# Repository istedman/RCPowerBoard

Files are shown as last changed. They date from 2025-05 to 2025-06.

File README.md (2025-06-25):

# RCPowerBoard

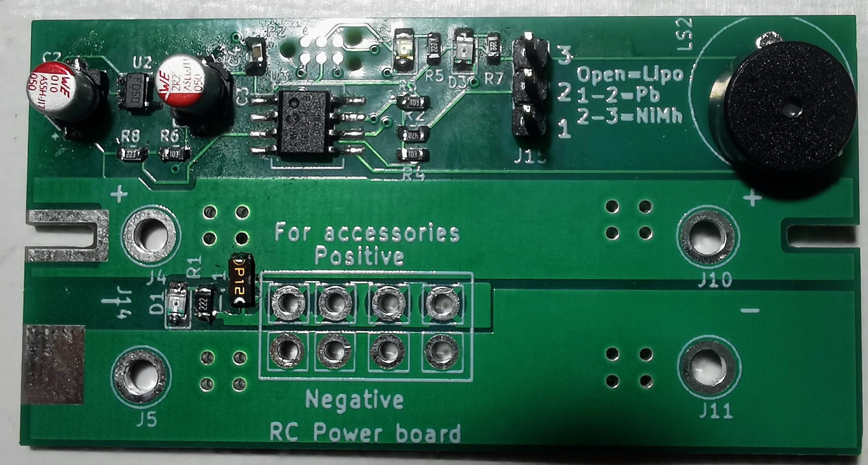
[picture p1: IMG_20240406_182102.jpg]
Photo of the PCB


A power distribution and battery monitor PCB for radio control vehicles. It can handle up to 15A, I use it on my smaller boats without issue.
Power connections are via plated through-hole or deans/T connectors. There are 4 pairs of smaller holes, connected via a 3.15A polyfuse, for accessory circuits. This protects the battery from short circuits in the accessory devices.

A PIC12F1840 microcontroller monitors the battery/cell voltages and when it gets too low, a buzzer will sound to let you know.

## Supported battery types

4-8 cell NiMh
1-3 cell Lipo
6V or 12V lead acid.

## Software
The design is minimal. A jumper identifies the battery type to monitor, providing you set this with a freshly charged battery pack, it will correctly determine the cell count and store the required settings in EEPROM. Only needs to be done once.
The BatteryMonitor.X directory contains the full source code, exported from MPLabX 6.20

**The software is designed to monitor the battery pack to these lower levels:**
_Lithium Polymer (LiPo)_
Single cell (1S) Lipo    3.6V
Duall cell (2S) Lipo     7.2V
Triple cell (3S) Lipo    10.8V
#define TRIPLE_LIPO_HIGH    12.600     // 12.6V

_Lead acid/AGM cell voltages_
 100% 2.12-2.15V per cell
 20% 1.93V/cell
 0% 1.75V/cell
 We will warn at 20% or 1.93V/cell
6V lower limit is  5.790V
12V lower limit is 11.580V     

_NiMH battery packs_
4 Cell NiMh    4.000V
5 Cell NiMh    5.000V    
6 Cell NiMh    6.00V
7 Cell NiMh    7.00V
8 Cell NiMh    8.00V

The software uses the internal A/D converter of the PIC microcontroller to sample the cell voltage, average it and if it drops below the limits detailed above, it will sound the buzzer. The A/D sampling is at a low rate, this was found to be effective in filtering out momentary supply blips when they accured, eliminating false failures.

Microchip Code Configurator (MCC) was used to setup the device and calibrate the internal voltage reference.

**Measured accuracy has been +/- 0.8% at room temperature** the 1% resistors used in the potential divider, contribute to the error in measurement, which was around 80mV in a 14V range.

## Known issues

The MCP2030 programming header is wrong, I had to swap signals around, will fix it in the next PCB iteration.
The deans/T connector footprint is off, again will be fixed in next revision.
The software only supports Nimh cells with even number of cells.
The PCB is bigger than it needs to be. I have 25 PCBs so there is no rush to fix the design, yet.

## Future development
A new, smaller design is in development that just monitors the battery and supports a wider range of chemistries/types. It can operate from a single cell Lipo or 3 NiMh cells. Plan to publish this later in the year, when finished.

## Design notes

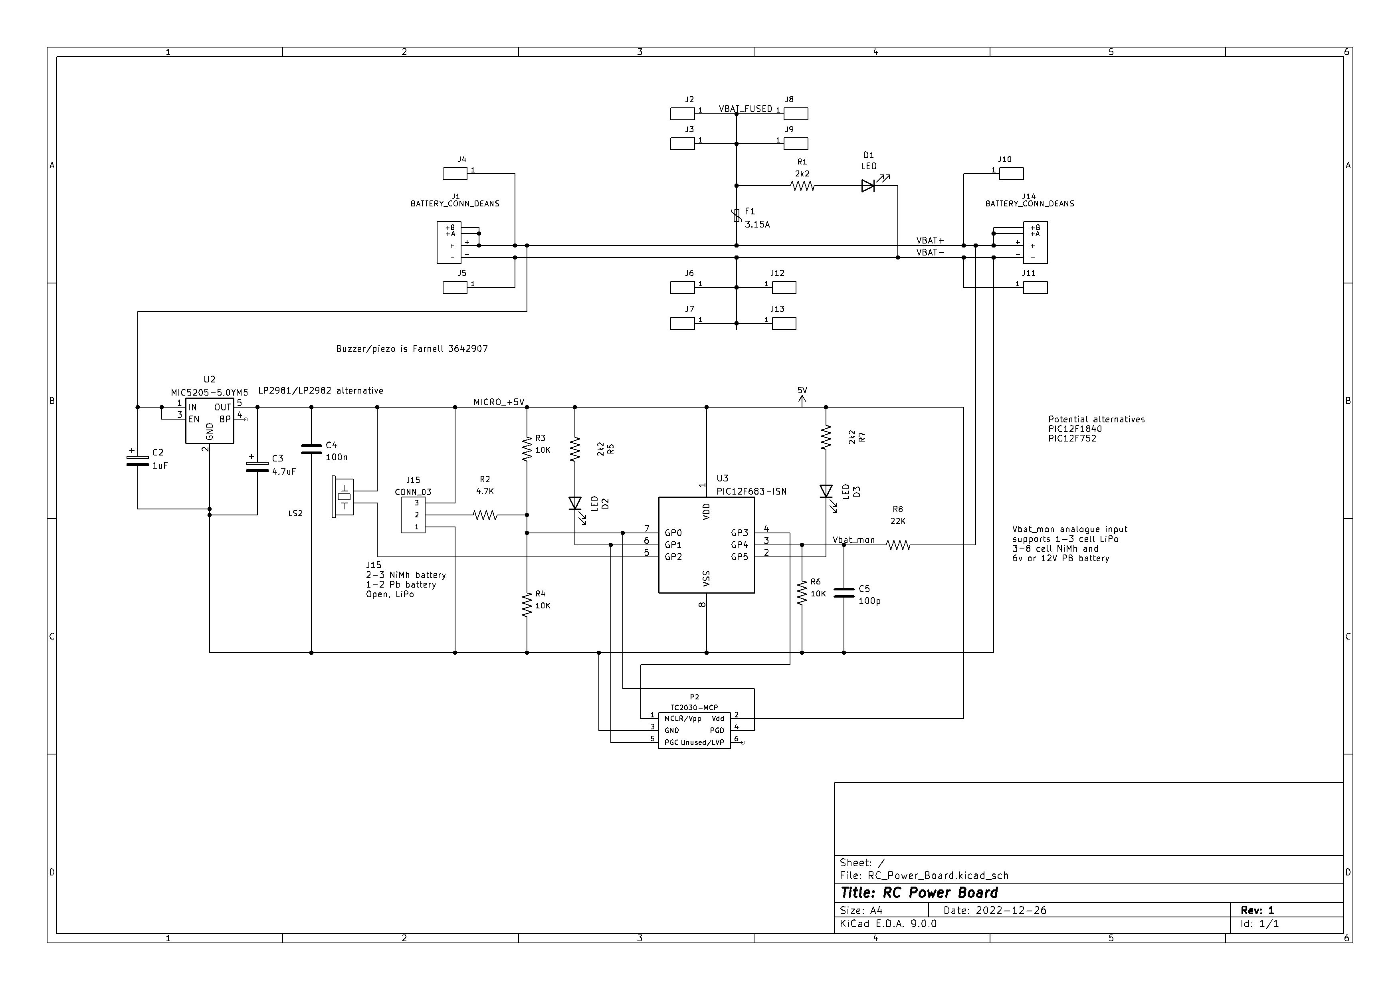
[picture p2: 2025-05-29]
RC_Power_board_schematic.jpg

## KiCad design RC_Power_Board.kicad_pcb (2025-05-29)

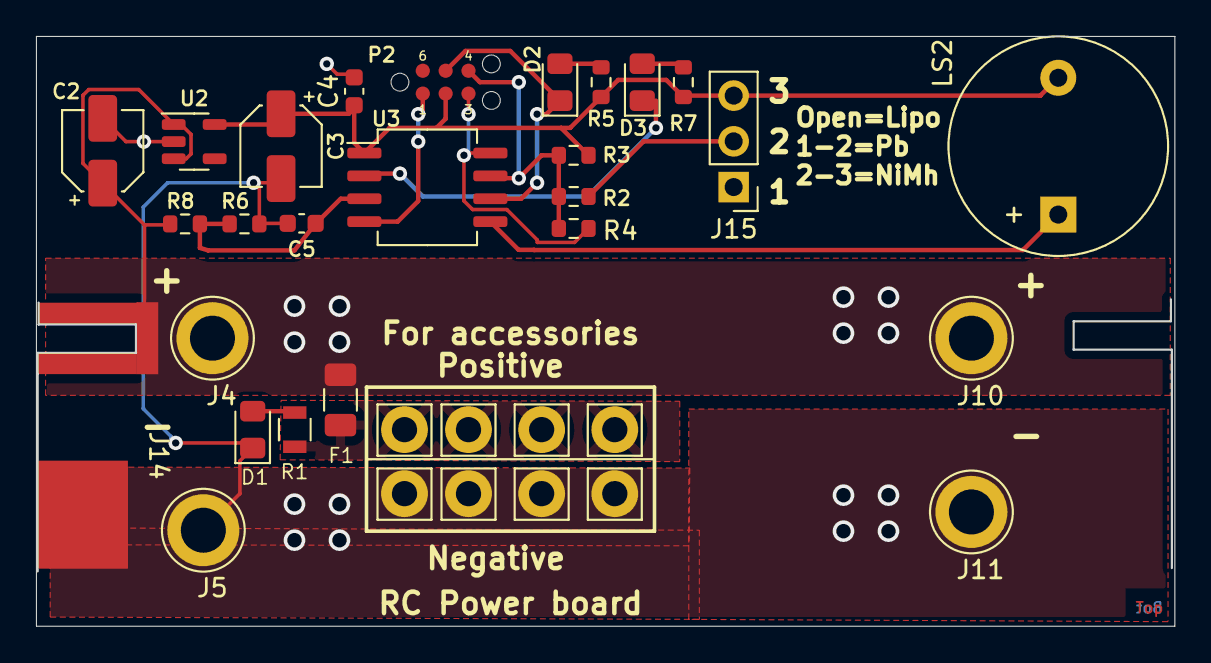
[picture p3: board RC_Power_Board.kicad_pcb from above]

Board: 2 copper layers, 63.2 x 32.8 mm, 35 parts (1 on the bottom side), 14 nets.

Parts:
C2: 1uF; CP_Elec_4x5.4
C3: 4.7uF; CP_Elec_4x5.4
C4: 100n; C_0603_1608Metric
C5: 100p; C_0603_1608Metric
D1, D2, D3: LED; LED_0805_2012Metric_Pad1.15x1.40mm_HandSolder
F1: 3.15A; Fuse_1206_3216Metric
J1, J14: BATTERY_CONN_DEANS; Deans_PCB
J2, J3, J6, J7, J8, J9, J12, J13: CONN_01POGOPIN_HOLE_LARGE; Pin_D1.4mm_L8.5mm_W2.8mm_FlatFork
J4, J5, J10, J11: CONN_01POGOPIN_HOLE_LARGE; TestPoint_Loop_D3.80mm_Drill2.5mm
J15: CONN_03; PinHeader_1x03_P2.54mm_Vertical
LS2: BUZZER-PTH; Buzzer_12x9.5RM7.6
P2: TC2030-MCP; TC2030-IDC-NL
R1: 2k2; R_0805
R2: 1K; R_0603_1608Metric
R3, R4, R6: 10K; R_0603_1608Metric
R5, R7: 2k2; R_0603_1608Metric
R8: 22K; R_0603_1608Metric
U2: MIC5205-5.0YM5; SOT-23-5
U3: PIC12F683-ISN; SO-8_5.3x6.2mm_P1.27mm

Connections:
/MICRO_+5V: C3.1, C4.1, J15.3, LS2.2 (-), P2.2 (Vdd), R3.2, R5.1, R7.1, U2.5 (OUT), U3.1 (VDD)
/VBAT+: C2.1, F1.2, J1.+, J4.1, J10.1, J14.+, R8.2, U2.1 (IN), U2.3 (EN)
/VBAT-: C2.2, C3.2, C4.2, C5.2, D1.1 (K), J1.-, J5.1, J6.1, J7.1, J11.1, J12.1, J13.1, J14.-, J15.1, P2.3 (GND), R4.1, R6.1, U2.2 (GND), U3.8 (VSS)
/VBAT_FUSED: F1.1, J2.1, J3.1, J8.1, J9.1, R1.1
/Vbat_mon: C5.1, R6.2, R8.1, U3.3 (GP4)
unnamed: D1.2 (A), R1.2
unnamed: D2.1 (K), P2.5 (PGC), U3.6 (GP1)
unnamed: D2.2 (A), R5.2
unnamed: D3.1 (K), U3.2 (GP5)
unnamed: D3.2 (A), R7.2
unnamed: J15.2, R2.2
unnamed: LS2.1 (+), U3.5 (GP2)
unnamed: P2.1 (MCLR/Vpp), U3.4 (GP3)
unnamed: P2.4 (PGD), R2.1, R3.1, R4.2, U3.7 (GP0)

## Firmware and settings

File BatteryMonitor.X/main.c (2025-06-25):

/**
  Generated Main Source File

  Company:
    Microchip Technology Inc.

  File Name:
    main.c

  Summary:
    This is the main file generated using PIC10 / PIC12 / PIC16 / PIC18 MCUs

  Description:
    This header file provides implementations for driver APIs for all modules selected in the GUI.
    Generation Information :
        Product Revision  :  PIC10 / PIC12 / PIC16 / PIC18 MCUs - 1.81.7
        Device            :  PIC12F1840
        Driver Version    :  2.00
*/


#include "mcc_generated_files/mcc.h"

#define LED1        LATAbits.LATA1  // RA0 is LED for debugging purposes
#define LED2        LATAbits.LATA5  // RA1 is second debug LED
#define BUZZER      LATAbits.LATA2
#define LEDON  0
#define LEDOFF 1
#define BUZZON 0
#define BUZZOFF 1
#define BUZZERON 10

//EEPROM locations
const unsigned char BAT_TYPE_STORE_LOC=0;
const unsigned char BAT_CELL_STORE_LOC=1;
#define BAT_TYPE_LIPO 0x10
#define BAT_TYPE_NIMH 0x20
#define BAT_TYPE_LEAD 0x30

//Initialise it for LIPO 2 Cell in EEPROM
__EEPROM_DATA(30,02,00,00,00,00,00,55);  

/*
 Based on 16V battery input range and a 10 bit ADC, the effective resolution is 15.625mV/bit
 The voltage seen at ADC input is 0.3125x the input voltage
 The Battery type analogue input uses the standard 4.88mV/bit resolution.
 * 
 */
// Might need to tweak single cell LiPO to use internal reference
#define SINGLE_LIPO_LOW     3.600     // 3.6V
#define SINGLE_LIPO_HIGH    4.250     // 4.25V
#define DUAL_LIPO_LOW       7.200     // 7.2V
#define DUAL_LIPO_HIGH      8.450     // 8.45V
#define TRIPLE_LIPO_LOW     10.800     // 10.8V
#define TRIPLE_LIPO_HIGH    12.600     // 12.6V

/* 
 Lead acid/AGM cell voltages
 * 100% 2.12-2.15V per cell
 * 20% 1.93V/cell
 * 0% 1.75V/cell
 * We will warn at 20% or 1.93V/cell
 */

#define LEAD_ACID_6V_LOW    5.790
#define LEAD_ACID_6V_HIGH   6.450    
#define LEAD_ACID_12V_LOW   11.580     
#define LEAD_ACID_12V_HIGH  12.900    


/* Might need to tweak 4 & 5 cell NiMh to use internal reference
 * Use 1.4V x number of cells for upper limit for battery detection
 * Use 1.2V for lower limit for detection, this is 50% charge for a cell
 * Use 1.0V x number of cells for lower limit 
 */

#define NIMH_4CELL_LOW      4.000    
#define NIMH_4CELL_DET_LOW  4.800
#define NIMH_4CELL_HIGH     5.600     

#define NIMH_5CELL_LOW      5.000    
#define NIMH_5CELL_DET_LOW  6.000
#define NIMH_5CELL_HIGH     7.000     

#define NIMH_6CELL_LOW      6.000     
#define NIMH_6CELL_DET_LOW  7.200
#define NIMH_6CELL_HIGH     8.400     

#define NIMH_7CELL_LOW      7.000     
#define NIMH_7CELL_DET_LOW  8.400
#define NIMH_7CELL_HIGH     9.600     

#define NIMH_8CELL_LOW      8.000     
#define NIMH_8CELL_DET_LOW  9.600
#define NIMH_8CELL_HIGH     11.200    








/*
 These voltages determine the battery type selected by the user.
 */

//#define DEBUG 12


#define BAT_NIMH_LOW        3.490 // 3.59V
#define BAT_NIMH_HIGH       4.070 // 3.97V
#define BAT_LIPO_LOW        2.275 // 2.375V
#define BAT_LIPO_HIGH       2.725 // 2.625V
#define BAT_PB_LOW          1.050 //1.15V
#define BAT_PB_HIGH         1.370 //1.27V

#define NUM_AVG 4

enum Bat_type {NIMH=10,PB=20,LIPO=30,UNKNOWN_BAT_TYPE=40};
enum Bat_config_type {SINGLE_LIPO=1,DUAL_LIPO=2,TRIPLE_LIPO=3, LEAD_ACID_6V=6,LEAD_ACID_12V=12,
NIMH_4CELL=40, NIMH_5CELL=50, NIMH_6CELL=60, NIMH_7CELL=70, NIMH_8CELL=80,UNKNOWN_CELL_COUNT=250};

enum Bat_type Battery_type=UNKNOWN_BAT_TYPE;
enum Bat_config_type Battery_Config=UNKNOWN_CELL_COUNT;
float LowerLimit=0,UpperLimit=1.0;
unsigned long Supply_Voltage, RefVoltage;
float ADC_Resn,vdd,BatteryVoltage,FBatSel; 



/*
 * Function to take NUM_AVG readings of the ADC and return the arithmetic mean
 * result. This should filter out noise
 
 */

//unsigned short Avg_ADC_GetConversion(unsigned short Channel)
float Avg_ADC_GetConversion(unsigned short Channel)
{
    unsigned short AveragedValue=0,AveragedResult=0;
    unsigned char ADCLoop;
    float ADCFloat=0.0;
    
    for (ADCLoop=0;ADCLoop<NUM_AVG;ADCLoop++)
    {
        AveragedValue+=ADC_GetConversion(Channel);
    }
    switch (NUM_AVG){
        case 2:
        {
            AveragedResult=AveragedValue >>1;
            break;
        }
        case 4:
        {
            AveragedResult=AveragedValue >>2;
            break;
        }
        case 8:
        {
            AveragedResult=AveragedValue >>3;
            break;
        }
    }
    if (Channel==BatSelect)
    {
        ADCFloat=(float)(ADC_Resn*AveragedResult);
        
    }
    else if (Channel==VBat)
    {
        ADCFloat=(float)(ADC_Resn/0.3125)*AveragedResult;
    }
    return (ADCFloat);
    }
 
/*
 * Function to read the voltage on the resistive divider and determine the battery
 * type. This is set by jumpers and the tolerances allow a ~5% variation for the 
 * onboard regulator.
 */

unsigned short DetermineBatType(void)
{
    FBatSel=Avg_ADC_GetConversion(BatSelect);
    
    if ((FBatSel>BAT_PB_LOW) && (FBatSel< BAT_PB_HIGH))
    {
        Battery_type=PB;
    }
    else if ((FBatSel>BAT_NIMH_LOW) && (FBatSel< BAT_NIMH_HIGH))
    {
        Battery_type=NIMH;
    }
    else if ((FBatSel>BAT_LIPO_LOW) && (FBatSel<BAT_LIPO_HIGH))
    {
        Battery_type=LIPO;
    }
    else
    {
        Battery_type=UNKNOWN_BAT_TYPE;
    }
#ifdef DEBUG
    Battery_type=NIMH;
#endif
    return(Battery_type);
}

unsigned char SoundBatAlarm(void)
{
#ifdef BUZZERON
    BUZZER=BUZZON;
    __delay_ms(500); //normally 300ms
    BUZZER=BUZZOFF;
    __delay_ms(500);
#else 
       LED1=LEDON;
       LED2=LEDON;
       __delay_ms(500);
       LED1=LEDOFF; 
       LED2=LEDOFF;
      __delay_ms(500);
#endif    
    return(1);
}

/*  Function to check the real time measured battery voltage, if outside of 
 * either test limit, we set Bealert to 1 to sound the alarm
 * 
 */

unsigned char CheckBatteryLevels(float MeasuredVoltage)
{
    unsigned char Bealert=0;
    float MeasVolt;
    MeasVolt=MeasuredVoltage;

    if((MeasVolt <LowerLimit) || (MeasVolt >UpperLimit))
	{
		Bealert=1;
	}
	else
	{
		Bealert=0;
	}
   return(Bealert);   
}

/*
 * Function to determine battery cell count based on measured voltage and type
 * The global BatteryVoltage, sampled before this function call, holds the current
 * calibrated battery voltage.
 */
unsigned char DetermineBatCellCount(void)
{
    unsigned short Batt_V=0;

    if (Battery_type == PB)
    {
        if (BatteryVoltage>=LEAD_ACID_6V_LOW && BatteryVoltage <= LEAD_ACID_6V_HIGH)
        {
            Battery_Config=LEAD_ACID_6V;
        }
        else if (BatteryVoltage>=LEAD_ACID_12V_LOW && BatteryVoltage <= LEAD_ACID_12V_HIGH)
        {
            Battery_Config=LEAD_ACID_12V;
        }
        else
        {
            Battery_Config=UNKNOWN_CELL_COUNT;
        }
    }
    else if (Battery_type == NIMH)
    {
        if (BatteryVoltage>=NIMH_4CELL_DET_LOW && BatteryVoltage <= NIMH_4CELL_HIGH )
        {
            Battery_Config= NIMH_4CELL;
        }
        else if (BatteryVoltage>=NIMH_6CELL_DET_LOW && BatteryVoltage <= NIMH_6CELL_HIGH )
        {
            Battery_Config= NIMH_6CELL;

        }
        else if (BatteryVoltage>=NIMH_8CELL_DET_LOW && BatteryVoltage <= NIMH_8CELL_HIGH )
        {
            Battery_Config= NIMH_8CELL;
          }
        else
        {
            Battery_Config=UNKNOWN_CELL_COUNT;
        }
    }
    
    else if (Battery_type == LIPO)
    {
        if (BatteryVoltage>=SINGLE_LIPO_LOW && BatteryVoltage <= SINGLE_LIPO_HIGH )
        {
            Battery_Config= SINGLE_LIPO;
        }
        else if (BatteryVoltage>=DUAL_LIPO_LOW && BatteryVoltage <= DUAL_LIPO_HIGH )
        {
            Battery_Config= DUAL_LIPO;
        }
        else if (BatteryVoltage>=TRIPLE_LIPO_LOW && BatteryVoltage <= TRIPLE_LIPO_HIGH )
        {
            Battery_Config= TRIPLE_LIPO;
        }
        else
        {
            Battery_Config=UNKNOWN_CELL_COUNT;
        }
        
    }
    
    return(Battery_Config);
}


unsigned int ReadFVR(void)
{
    unsigned int Vrefread=0;
    Vrefread=ADC_GetConversion(channel_FVR);
    return(Vrefread);
}

/*  Function to calibrate the ADC based on a read of the internal Fixed Voltage
 *  Reference (FVR) which is used to scale the power supply voltage, from this
 *  we determine the resolution of each ADC bit.
 */
unsigned char CalibrateADC(void)
{
  RefVoltage=ReadFVR();
    
/* Fixed point
    vdd = (65535 / SupplyVoltage) <<4;
*/    
    vdd = (float)((1024.0 /RefVoltage) * 1.024);
    ADC_Resn=vdd/1024;
}

/*  Function used to set the test limits for the battery. Providing the jumper
 * for battery type is correct, this should set the correct limits.
 */

unsigned char Set_Test_Limits(enum Bat_type Battery_Chemistry ,enum Bat_config_type Battery_Cell_Count)
{
    unsigned char numblinks=0;    
    unsigned char Cells=0;
    if (Battery_Chemistry == PB)
        {
        
            if (Battery_Cell_Count==LEAD_ACID_6V)
            {
                LowerLimit=LEAD_ACID_6V_LOW;
                UpperLimit=LEAD_ACID_6V_HIGH;
                numblinks=1;
            }
            else if (Battery_Cell_Count==LEAD_ACID_12V)
            {
                LowerLimit=LEAD_ACID_12V_LOW;
                UpperLimit=LEAD_ACID_12V_HIGH;
                numblinks=2;
            }
            
            for (Cells=0;Cells<numblinks;Cells++)
            {
                LED1=LEDON;
                __delay_ms(500);
                LED1=LEDOFF;
                __delay_ms(500);
            }
            //Now leave LED type indicator on throughout
            __delay_ms(1000);
            LED1=LEDON;
            LED2=LEDOFF;
        }
        
    else if (Battery_Chemistry == NIMH)
        {
            if (Battery_Cell_Count== NIMH_4CELL)
            {
                LowerLimit=NIMH_4CELL_LOW;
                UpperLimit=NIMH_4CELL_HIGH;
                numblinks=4;
            }
            else if (Battery_Cell_Count== NIMH_6CELL)
            {
                LowerLimit=NIMH_6CELL_LOW;
                UpperLimit=NIMH_6CELL_HIGH;
                numblinks=6;
            }
            else if (Battery_Cell_Count==NIMH_8CELL )
            {
                LowerLimit=NIMH_8CELL_LOW;
                UpperLimit=NIMH_8CELL_HIGH;
                numblinks=8;
            }
            for (Cells=0;Cells<numblinks;Cells++)
            {
                LED2=LEDON;
                __delay_ms(500);
                LED2=LEDOFF;
                __delay_ms(500);
            }
               
        //Permanent LED status
        __delay_ms(1000);
        LED1=LEDOFF;
        LED2=LEDON;
        }
    else if (Battery_Chemistry == LIPO)
    {
        if (Battery_Cell_Count==SINGLE_LIPO )
        {
            LowerLimit=SINGLE_LIPO_LOW;
            UpperLimit=SINGLE_LIPO_HIGH;
            numblinks=1;
        }
        else if (Battery_Cell_Count==DUAL_LIPO)
        {
            LowerLimit=DUAL_LIPO_LOW;
            UpperLimit=DUAL_LIPO_HIGH;
            numblinks=2;
        }
        else if (Battery_Cell_Count==TRIPLE_LIPO)
        {
            LowerLimit=TRIPLE_LIPO_LOW;
            UpperLimit=TRIPLE_LIPO_HIGH;
            numblinks=3;
        }
     
          for (Cells=0;Cells<numblinks;Cells++)
        {
             LED1=LEDON;
             LED2=LEDON;
            __delay_ms(500);
            LED1=LEDOFF; 
            LED2=LEDOFF;
            __delay_ms(500);
        }
          
        __delay_ms(1000);
        LED1=LEDON;
        LED2=LEDON;
    }
    return(1);
}


/*
                         Main application
 */
void main(void)
{
    unsigned char Alert=0;
    unsigned short RawBatVolt=0;
    unsigned char BatType_Stored=0,CellCount_Stored=99;

    // initialize the device
    SYSTEM_Initialize();
    // Ensure LEDs are off but sound buzzer for 500ms
    BUZZER=BUZZON;
    LED1=LEDOFF;
    LED2=LEDOFF;
    __delay_ms(500); 
    BUZZER=BUZZOFF;
    
    ADC_Initialize();
    CalibrateADC();
      
    
    //Recall settings from EEPROM, see if they match current settings
    BatType_Stored=eeprom_read(BAT_TYPE_STORE_LOC);
    CellCount_Stored=eeprom_read(BAT_CELL_STORE_LOC);  
    
    //Get a read of the battery to determine the type
    BatteryVoltage=Avg_ADC_GetConversion(VBat);
    DetermineBatType(); // Determine type and flash LEDs
    //__delay_ms(500);            
    Battery_Config=DetermineBatCellCount();
    
      /*If current settings do not match those stored, update the stored settings 
      and set the cell count. 
     */
    if(BatType_Stored!=Battery_type)
    {
      eeprom_write(BAT_TYPE_STORE_LOC,Battery_type);
      eeprom_write(BAT_CELL_STORE_LOC,Battery_Config); 
    }
    
    /* This is to capture a flat battery and sound the alarm, based on the stored settings.
     * A flat battery should return a UNKNOWN_CELL_COUNT so we used the saved
     * settings from the EEPROM.
     */
    if (Battery_Config==UNKNOWN_CELL_COUNT)
    {
        Battery_Config=CellCount_Stored;
    }
    
    Set_Test_Limits(Battery_type,Battery_Config);

    while (1)
    {
        BatteryVoltage=Avg_ADC_GetConversion(VBat);
        Alert=CheckBatteryLevels(BatteryVoltage);
        if (Alert==1)
        {
            SoundBatAlarm();
        }
        __delay_ms(25);
        
    }
}
/**
 End of File
*/
